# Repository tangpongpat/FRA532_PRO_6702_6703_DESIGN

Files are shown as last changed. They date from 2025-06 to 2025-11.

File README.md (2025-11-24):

## Drift Concept

Drifting is a driving technique that involves intentionally inducing **oversteer**, causing a loss of traction in the rear wheels while maintaining control throughout a corner. In this project, we focus on enabling controlled drift by tuning the balance between **traction**, **power**, and **braking force**, especially with a **rear-wheel drive (RWD)** configuration.

<p align="center">
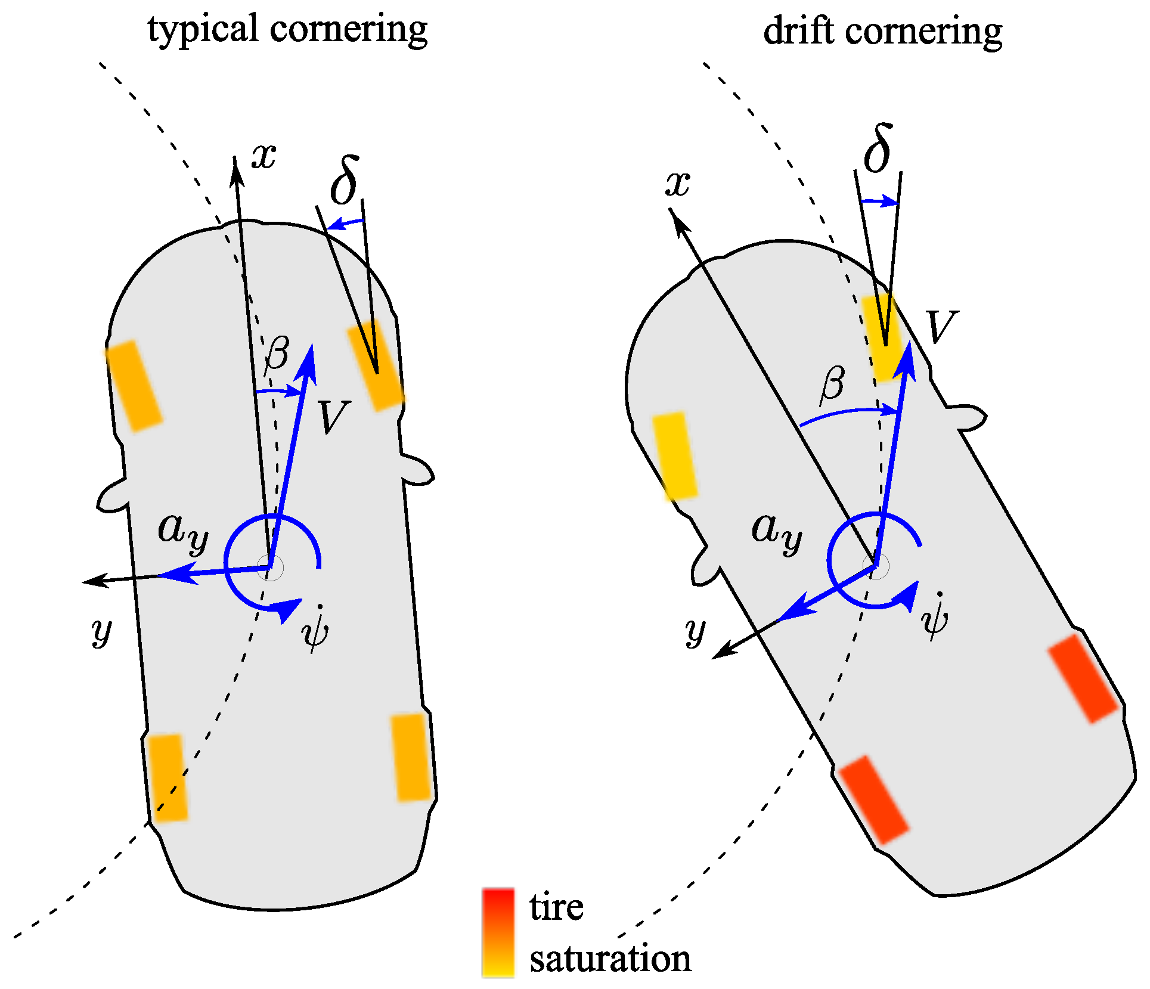
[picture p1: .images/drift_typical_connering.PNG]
Drift vs Typical Cornering
    
</p>

- In **typical cornering**, the front tires steer in the direction of the curve while the rear tires maintain grip.
- In **drift cornering**, the car rotates into the turn with the **rear tires saturated**, sliding outward, while the front wheels counter-steer to guide the direction.
- The vehicle exhibits a **high sideslip angle (β)** and controlled **yaw rate (ψ)**, while lateral acceleration (**aᵧ**) still points toward the center of the curve.

## Things to Consider

- Rear tire traction is intentionally reduced to initiate drift.
- Front tires must maintain enough grip for counter-steering control.
- Weight transfer helps unsettle the rear end.
- Tire compound and surface friction significantly affect driftability.
- Balance between motor torque and braking response is critical for stable drift control.

## Transmisstion system
Originally based on an all-wheel-drive (AWD) layout, the F1TEETH platform has been modified to **rear-wheel drive (RWD)** to improve the ability to break traction at the rear wheels. This configuration allows better control over drifting behavior and enables intentional oversteer, which is essential for sustained drifts.

To achieve this, the **driveshaft connecting the motor to the front wheels was removed**, effectively disabling the front-wheel drive and converting the system into a purely rear-wheel-driven platform.

## Braking System
I chose to use a magnetic braking system because it requires the **least amount of space for installation**, especially compared to traditional servo-based brakes, which are often bulky. The magnetic setup is also **lighter in weight**, making it more suitable for small-scale RC vehicles. Additionally, this design allows for the possibility of implementing **ABS-like behavior**, helping the car come to a stop smoothly and precisely with minimal wheel lock-up.

## Schematic & Wiring Diagram

<p align="center">
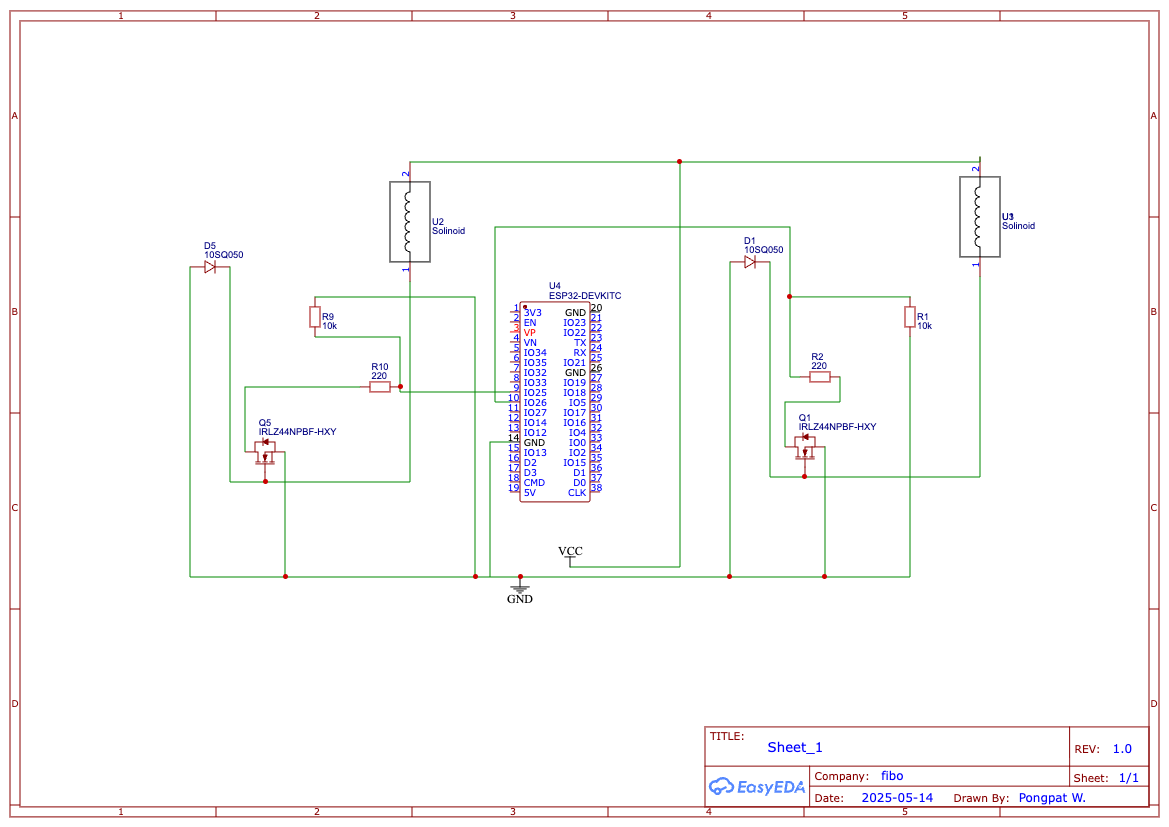
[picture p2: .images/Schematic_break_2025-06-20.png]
schematic
    
</p>

<p align="center">
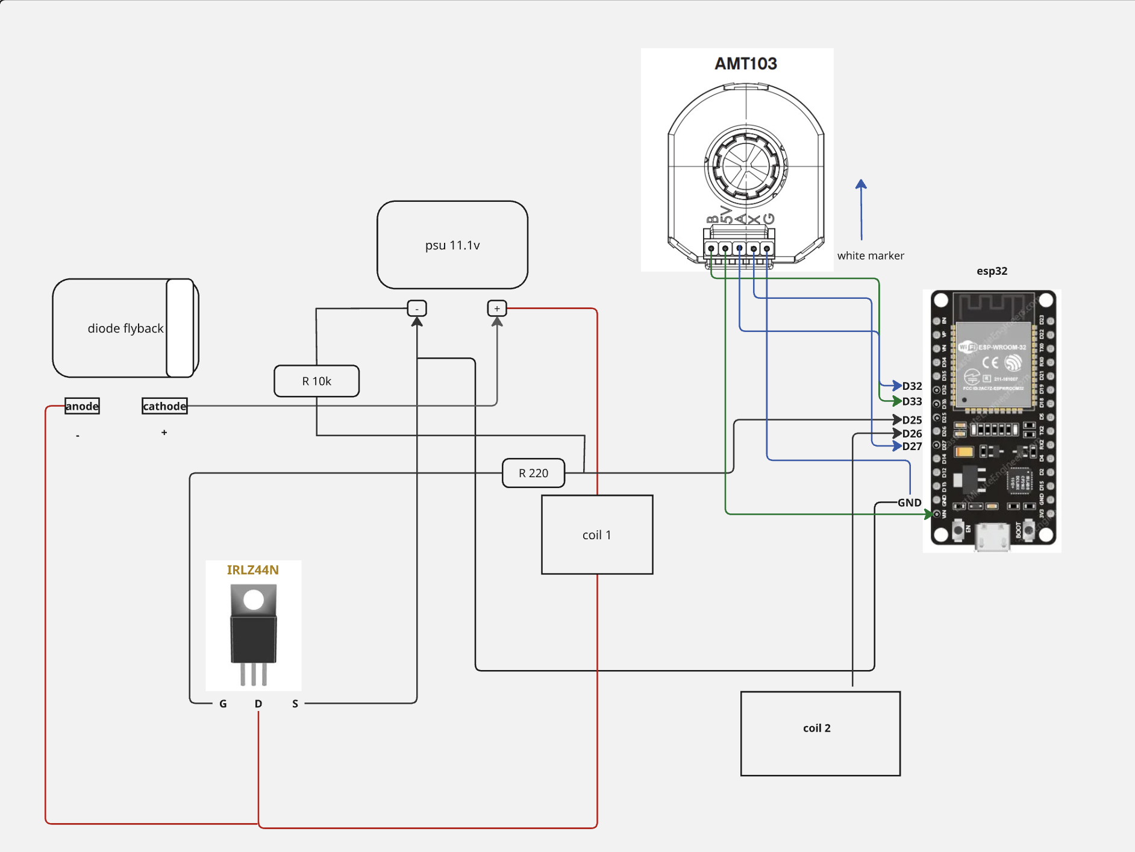
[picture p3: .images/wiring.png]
wiring
    
</p>

<p align="center">
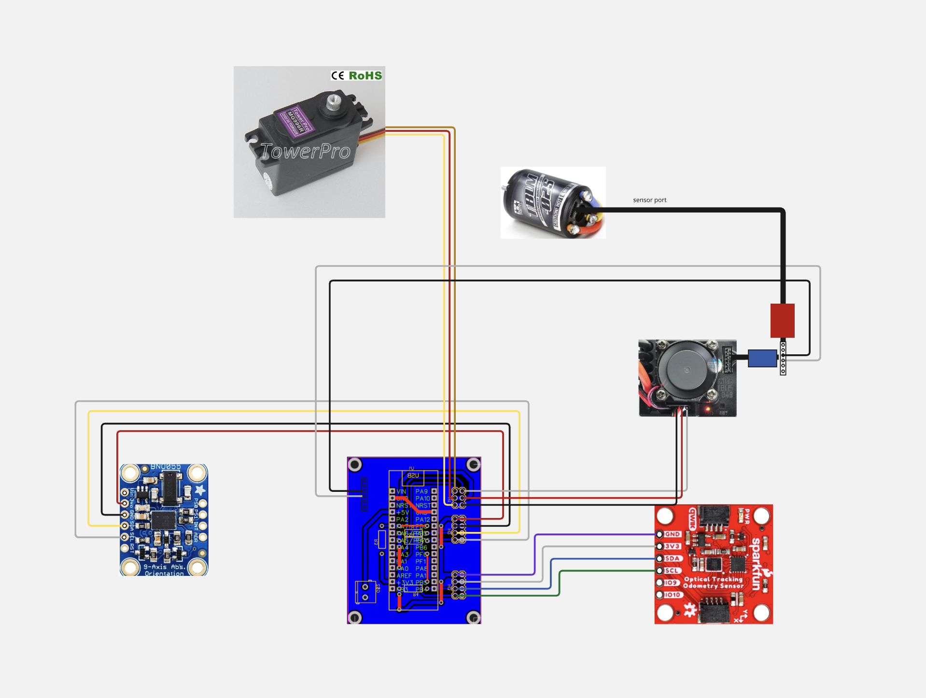
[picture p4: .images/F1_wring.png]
    
</p>

<!-- * **Braking Schematic:** [Braking Schematic](/.images/Schematic_break_2025-06-20.png) -->

### Drum Brake Specifications
| Property | Value |
|---|---|
| Outer Diameter | 14.5 mm |
| Drump Thickness | 3 mm |
| Axial Length | 15.6 mm |

### Coil Specifications

| Property | Value |
| --- | --- |
| Core Type | Steel |
| Outer Diameter | 12 mm |
| Inner Diameter | 8 mm |
| Wire Used | 0.5 mm magnet wire |
| Power | 12V DC |
| Resistance | \~1.5 Ω |
| Current | \~8 A |
| Application Load | \~2 kg |

### Magnetic Force Estimation

| Symbol | Value | Description |
| --- | --- | --- |
| N | 270 turns | Number of coil windings |
| I | 8 A | Coil current |
| A | 1.13 × 10⁻⁴ m² | Core area (radius = 6 mm) |
| g | 0.0003 m | Air gap (0.3 mm) |
| μᵣ | 1000 | Relative permeability (steel) |
| μ₀ | 4π × 10⁻⁷ H/m  | Vacuum permeability constant  |

$$
F = \frac{N^2 \cdot \mu \cdot A \cdot I^2}{2 \cdot g^2}
$$

***Estimated force:** 60 N at full load > RC car mass 3 KG

## Tesing & Result 

### Front vs Rear Wheel Understeering

The following videos demonstrate the difference in understeering behavior between front-wheel and rear-wheel drive configurations:

- [Front wheel understeering F1TEETH](https://youtu.be/fvo7P59drMA) — In front-wheel drive, **understeer typically requires braking** to shift the weight forward and reduce rear traction. Without braking, the front wheels tend to maintain grip, limiting the ability to rotate the vehicle.
- [Rear wheel understeering F1TEETH](https://youtu.be/cZtpaluhPYI) — In rear-wheel drive, the car can **naturally induce understeer without braking**, due to rear torque overpowering traction. This makes it easier to break rear grip and start a drift even without applying the brake.

### 🧪 Inertial Braking Test Results

To test the effectiveness of each braking method, the car was released from a fixed starting point and allowed to accelerate under consistent conditions. The braking system was activated when the car reached a marked finish line. Two braking methods were compared:

1. **ESC Brake** — electronic braking via the speed controller
2. **Coil Brake** — electromagnetic braking using the custom coil 

| Attempt | ESC Brake Distance | Coil Brake Distance |
|---|---|---|
| 1 | 290 mm | 144 mm |
| 2 | 280 mm | 180 mm |
| 3 | 300 mm | 165 mm |

**Observation:**  
The coil brake consistently results in shorter stopping distances, confirming its ability to reduce rotational inertia more effectively than standard ESC braking. This allows the car to enter drift states more predictably and stop in tighter spaces.

### Known Issues (MK I)

* **1.1** Mount misalignment between the coil’s actuator surface and the brake dump

<p align="center">
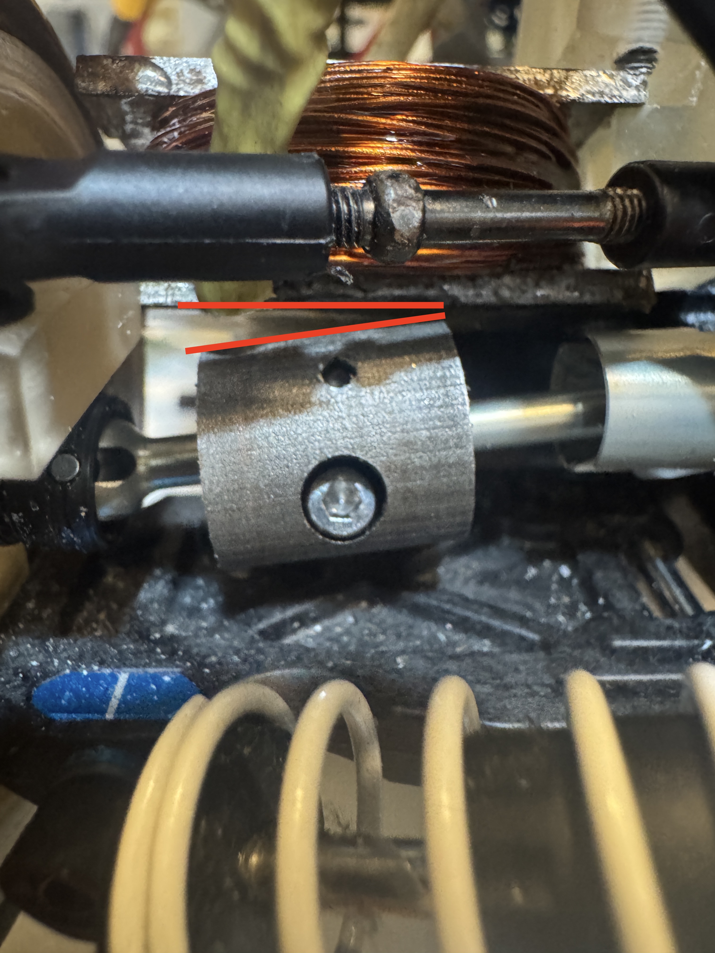
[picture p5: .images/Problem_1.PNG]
coil
    
</p>

### undone

- [ ] Connect circuit board with opto-isolate
- [ ] Front Break
- [ ] replace DIY Board with pcb 
- [ ] Reposition the shock absorber mounting
- [ ] Minimize backlash on steering ackermann 
- [ ] wisted pair for magnetic shielding
## Ref

[A Torque Vectoring Control for Enhancing Vehicle Performance in Drifting](https://www.mdpi.com/2079-9292/7/12/394)

[How To Winding the Magnet Wire](https://www.instructables.com/POWERFUL-ELECTROMAGNET-5KG-LIFTING/)

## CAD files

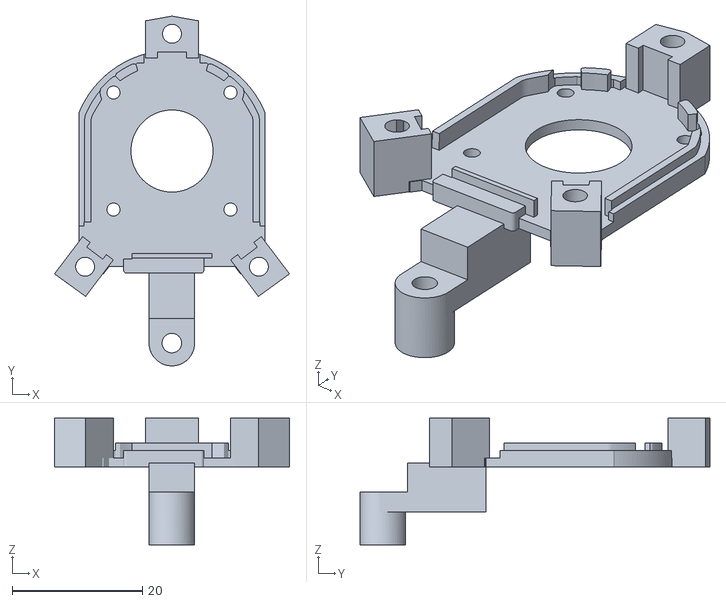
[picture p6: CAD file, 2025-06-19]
CAD/ABS/encoder_mount.stl
36.1 x 53.7 x 19.5

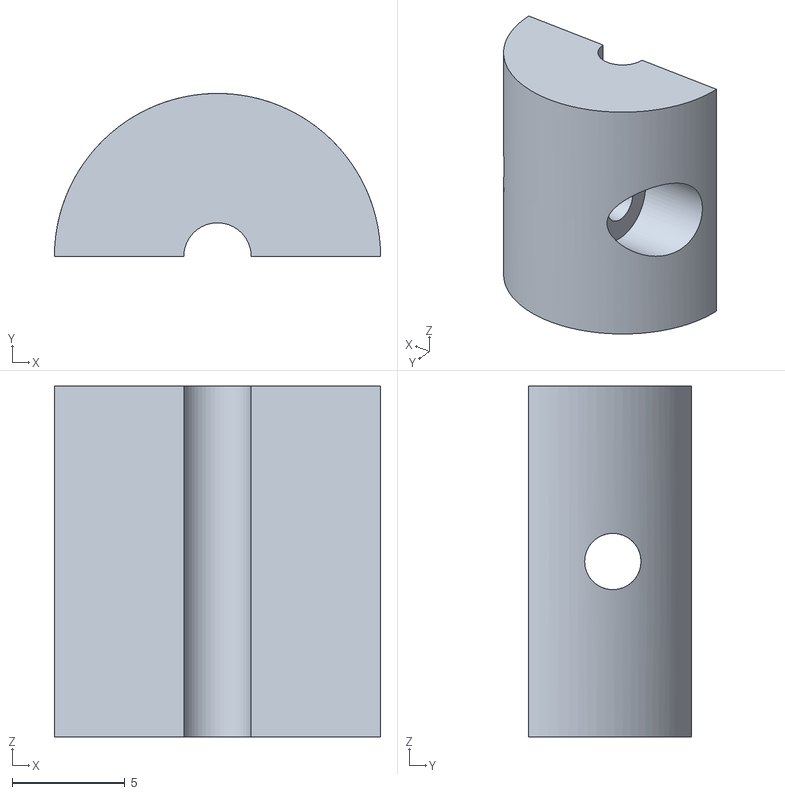
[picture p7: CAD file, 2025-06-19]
CAD/STEEL/dump.stl
14.5 x 7.25 x 15.6

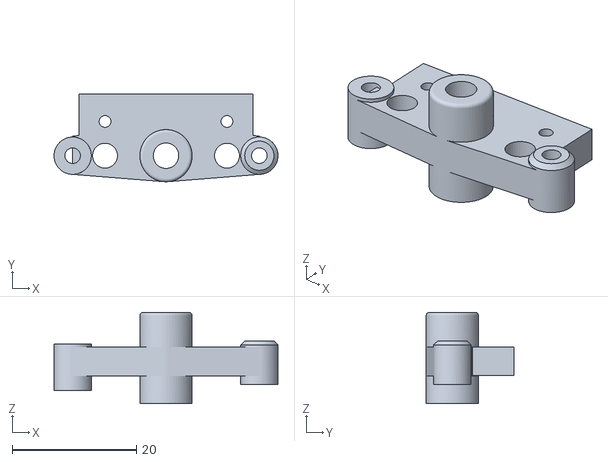
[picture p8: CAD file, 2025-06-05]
CAD/ABS/steering_mount_right.stl
36.0 x 14.1 x 14.7

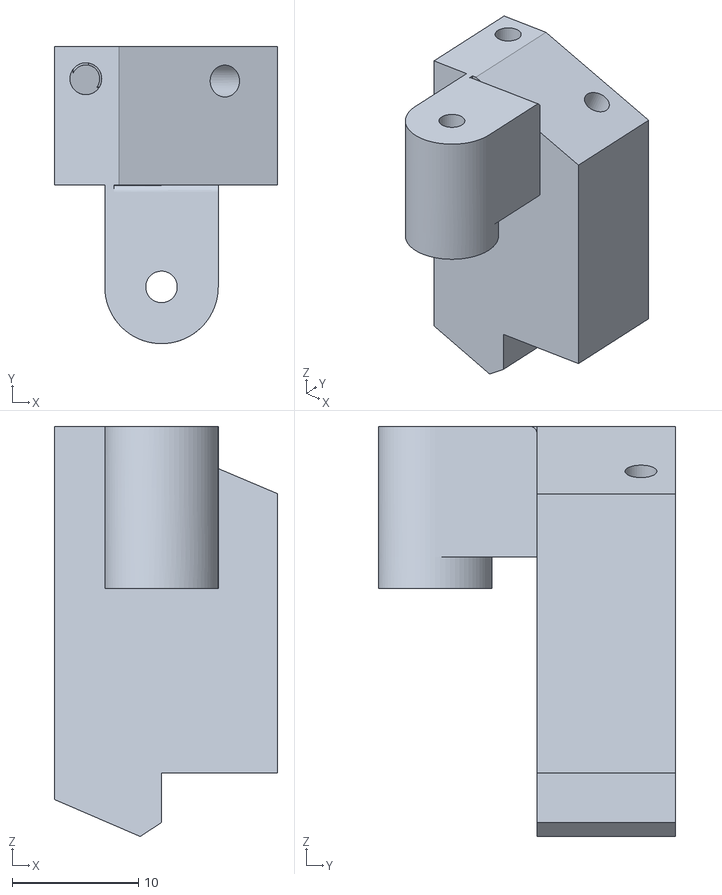
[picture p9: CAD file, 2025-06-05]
CAD/STEEL/coil_mount_rear_left.stl
17.7 x 23.6 x 32.5

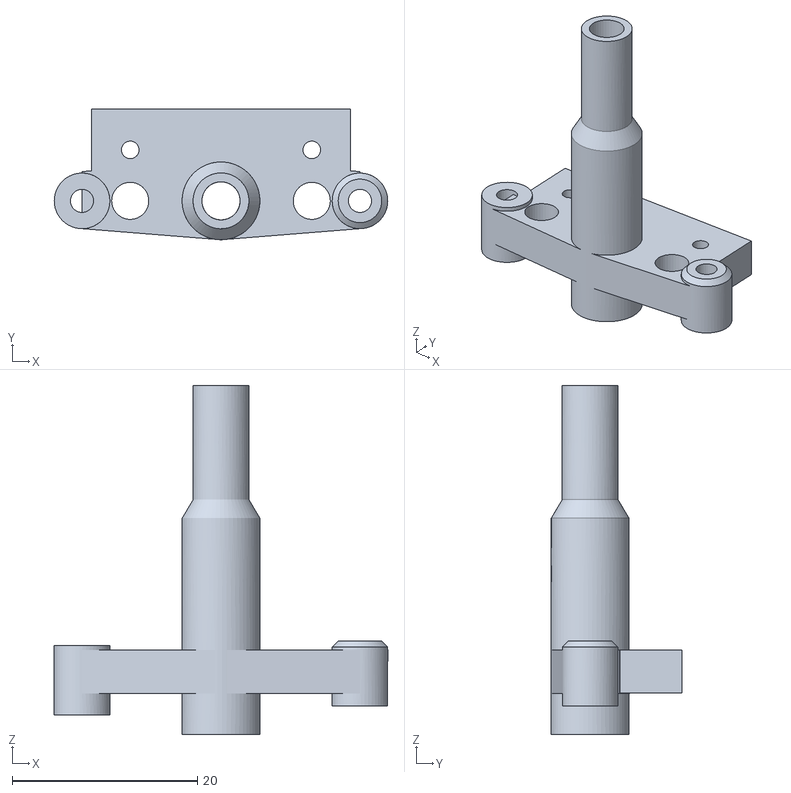
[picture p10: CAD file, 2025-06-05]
CAD/ABS/steering_mount_left.stl
36.0 x 14.1 x 37.7

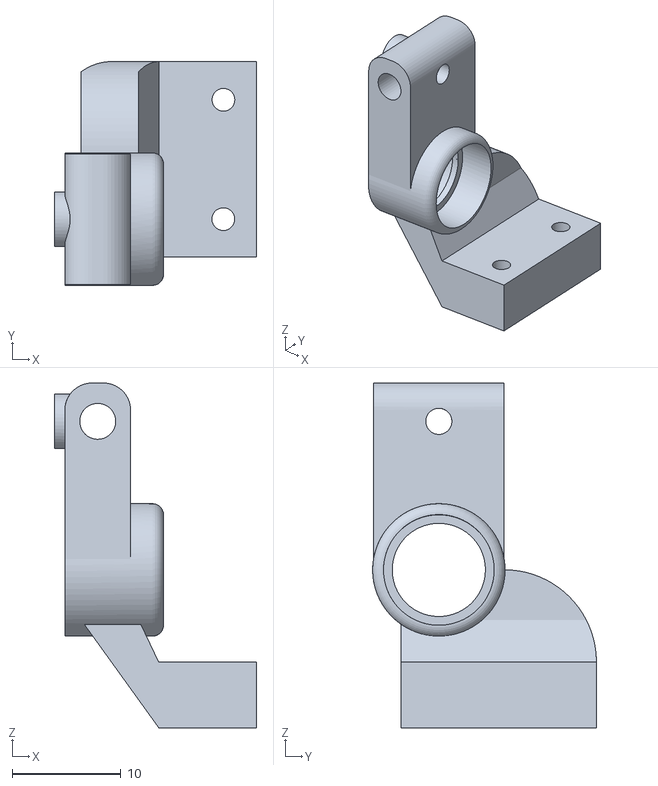
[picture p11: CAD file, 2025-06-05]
CAD/ABS/WHEEL_MOUNT_REAR_RIGHT.stl
18.6 x 20.5 x 31.7

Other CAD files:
CAD/STEEL/coil_mount_rear_right.stl
CAD/ABS/WHEEL_MOUNT_REAR_LEFT.stl

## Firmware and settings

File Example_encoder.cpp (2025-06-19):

#include <Arduino.h>

// — encoder pin definitions —
// Connect your AMT103 A & B outputs here
const int encoderPinA = 32;  // GPIO32 → Channel A
const int encoderPinB = 33;  // GPIO33 → Channel B

// — state variables —
// encoderCount holds the current position (can be + or –)
volatile long encoderCount = 0;
// lastEncoded stores the previous (A,B) state as two bits
volatile byte lastEncoded = 0;

// — interrupt routine to update encoderCount —
// must be in IRAM on ESP32 for fastest response
void IRAM_ATTR updateEncoder() {
  // read both channels
  byte MSB = digitalRead(encoderPinA);
  byte LSB = digitalRead(encoderPinB);
  byte encoded = (MSB << 1) | LSB;

  // combine previous and current state into a 4-bit number
  byte sum = (lastEncoded << 2) | encoded;

  // depending on the transition, increment or decrement
  if (sum == 0b1101 || sum == 0b0100 || sum == 0b0010 || sum == 0b1011) {
    encoderCount++;
  }
  else if (sum == 0b1110 || sum == 0b0111 || sum == 0b0001 || sum == 0b1000) {
    encoderCount--;
  }

  // save this state for next interrupt
  lastEncoded = encoded;
}

void setup() {
  // start serial for output
  Serial.begin(115200);

  // configure pins with pull-ups (encoder outputs are open-collector)
  pinMode(encoderPinA, INPUT_PULLUP);
  pinMode(encoderPinB, INPUT_PULLUP);

  // read the initial state of encoder pins
  byte MSB = digitalRead(encoderPinA);
  byte LSB = digitalRead(encoderPinB);
  lastEncoded = (MSB << 1) | LSB;

  // attach interrupts on both channels
  attachInterrupt(digitalPinToInterrupt(encoderPinA), updateEncoder, CHANGE);
  attachInterrupt(digitalPinToInterrupt(encoderPinB), updateEncoder, CHANGE);
}

void loop() {
  // capture and print the count every 100ms
  static long lastPrint = 0;
  if (millis() - lastPrint > 100) {
    lastPrint = millis();
    noInterrupts();
    long pos = encoderCount;
    interrupts();

    Serial.print("Encoder count = ");
    Serial.println(pos);
  }
}

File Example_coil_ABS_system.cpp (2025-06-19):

#include <Arduino.h>

const int COIL1_PIN = 25;
const int COIL2_PIN = 26;
const int PWM_CH1    = 0;
const int PWM_CH2    = 1;
const int PWM_FREQ   = 1000;  // 1 kHz
const int PWM_RES    = 8;     // 8-bit
const int DUTY_50    = 120;   // 50% duty max 225

// Pulse parameters (in ms):
const uint16_t ON_TIME_MS  = 10;  // coil on for 10 ms
const uint16_t OFF_TIME_MS = 5;  // coil off for 20 ms

void setup() {
  ledcSetup(PWM_CH1, PWM_FREQ, PWM_RES);
  ledcAttachPin(COIL1_PIN, PWM_CH1);

  ledcSetup(PWM_CH2, PWM_FREQ, PWM_RES);
  ledcAttachPin(COIL2_PIN, PWM_CH2);
}

void loop() {
  // — ON phase —
  ledcWrite(PWM_CH1, DUTY_50);
  ledcWrite(PWM_CH2, DUTY_50);
  delay(ON_TIME_MS);

  // — OFF phase —
  ledcWrite(PWM_CH1, 0);
  ledcWrite(PWM_CH2, 0);
  delay(OFF_TIME_MS);
}
